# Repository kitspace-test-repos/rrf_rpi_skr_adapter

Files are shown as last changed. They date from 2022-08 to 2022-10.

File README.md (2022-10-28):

Raspberry Pi to SKR/SKR Pro Adapter for ReprapFirmware
======================================================

The adapter sold by TeamGloomy on Tindie for this purpose is sold out.  This
is my equivalent replacement.

Description
-----------

I'm looking at putting ReprapFirmware on my Hypercube 300.  The necessary
adapter to connect its Raspberry Pi Zero 2 W to its SKR Pro 1.2 is
out-of-stock on Tindie.  This is a smaller adapter that does the same thing,
only it plugs into the EXP2 header on the printer motherboard and a 6-wire
cable connects the other end to pins 19-24 on the Raspberry Pi GPIO header. 
(I already have a 4-wire UART connection between the two that also supplies
power; instead of putting in the full 40-pin GPIO header, it only has enough
pins populated for the connections I'm using.)

It was a quick layout to throw together in KiCad; I probably spent more time
playing around with panelization options than on the main layout.  :) I
should have 100 (20x5) bare boards arriving from JLCPCB, and the parts to go
on it are dirt-cheap…should be well under $5 from DigiKey, and probably
under $1 each in quantity from LCSC.

This project is also on
[printables.com](https://www.printables.com/model/262089-raspberry-pi-to-skrskr-pro-adapter-for-reprapfirmw).

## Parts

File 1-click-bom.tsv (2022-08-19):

References | Qty | Description | DigiKey_SKU | Inv_ID | LCSC_SKU | MPN | Manufacturer | Mouser_SKU | Notes | Package
J1 | 1 | Connector Header Through Hole, Right Angle 2x3 position 0.100" (2.54mm) | 2057-PH2RA-06-UA-ND | 60 | C706884 | PH2RA-06-UA | Adam Tech |  | LCSC SKU is substitute:: XKB X6521WR-2x03H-C30D60
J2 | 1 | 2x5 Position Header Connector 0.100" (2.54mm) Through Hole, Right Angle Gold | S9202-ND | 61 | C239356 | SFH11-PBPC-D05-RA-BK | Sullins Connector Solutions |  | LCSC SKU is substitute: CJT A2541HWR-2x5P
R1, R2, R3, R4, R5 | 5 | 100 Ω 0603 resistor | 311-100HRCT-ND | 49 | C105588 | RC0603FR-07100RL | Yageo | 603-RC0603FR-07100RL |  | 0603

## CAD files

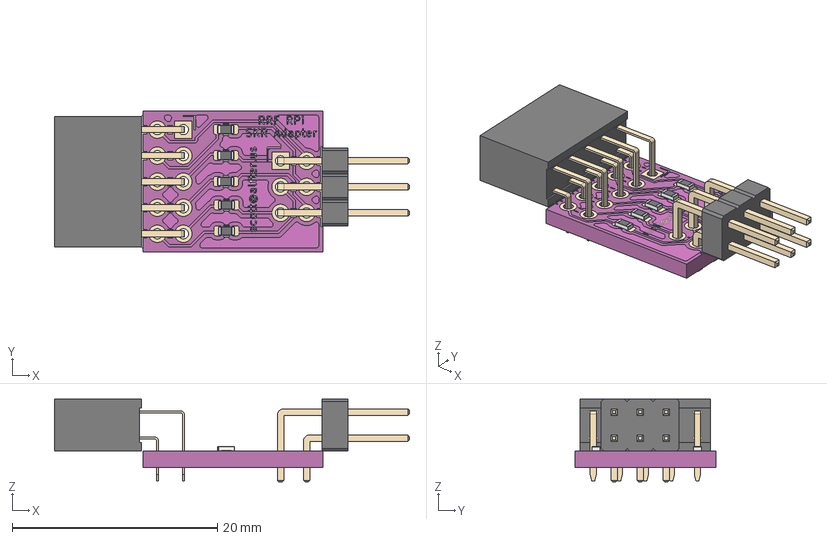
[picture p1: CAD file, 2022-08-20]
rrf_rpi_skr_adapter.step
34.6 x 13.7 x 8.08 mm
Pcb_c4a0
topPads_c4a0
topTracks_c4a0
topZones_c4a0
botPads_c4a0
botZones_c4a0
topSilks_d746
R5_R_0603_1608Metric_efb6d9ae4d17 x 5
J2_PinSocket_2x05_P254mm_Horizontal_7ad49dfecfbd
J1_PinHeader_2x03_P254mm_Horizontal_a65a8578a4f9

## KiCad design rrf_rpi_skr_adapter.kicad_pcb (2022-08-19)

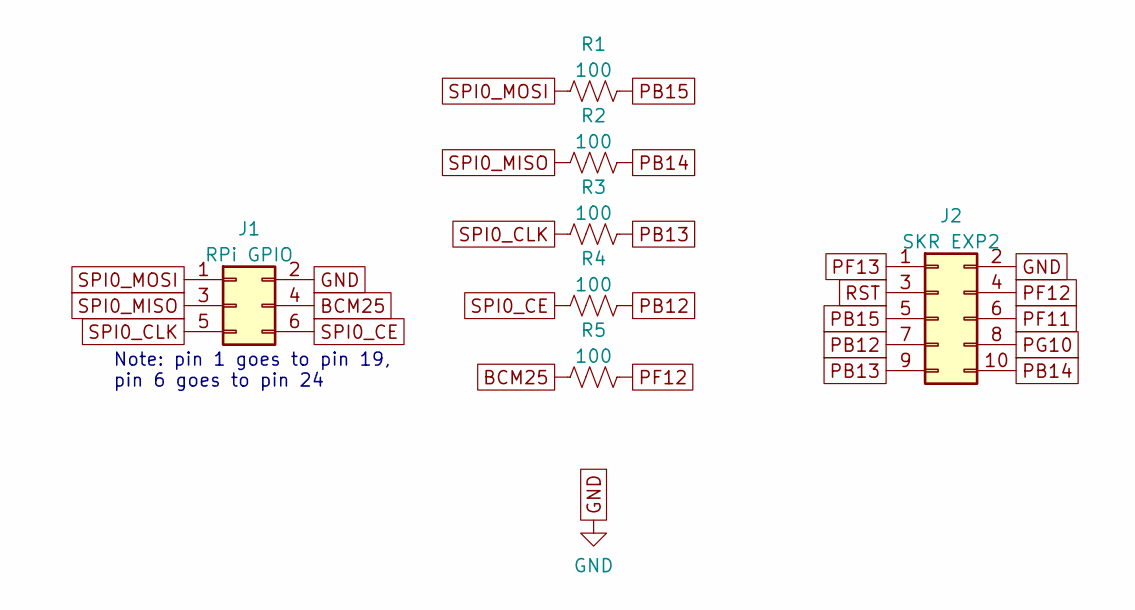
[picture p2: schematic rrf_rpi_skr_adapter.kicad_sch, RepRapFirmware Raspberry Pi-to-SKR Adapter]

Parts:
J1: RPi GPIO; PinHeader_2x03_P2.54mm_Horizontal; MPN PH2RA-06-UA; DigiKey_SKU 2057-PH2RA-06-UA-ND
J2: SKR EXP2; PinSocket_2x05_P2.54mm_Horizontal; MPN SFH11-PBPC-D05-RA-BK; DigiKey_SKU S9202-ND
R1, R2, R3, R4, R5: 100; R_0603_1608Metric; MPN RC0603FR-07100RL; DigiKey_SKU 311-100HRCT-ND

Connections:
BCM25: J1.4, R5.1
GND: J1.2, J2.2
PB12: J2.7, R4.2
PB13: J2.9, R3.2
PB14: J2.10, R2.2
PB15: J2.5, R1.2
PF11: J2.6
PF12: J2.4, R5.2
PF13: J2.1
PG10: J2.8
RST: J2.3
SPI0_CE: J1.6, R4.1
SPI0_CLK: J1.5, R3.1
SPI0_MISO: J1.3, R2.1
SPI0_MOSI: J1.1, R1.1

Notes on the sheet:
Note: pin 1 goes to pin 19, pin 6 goes to pin 24

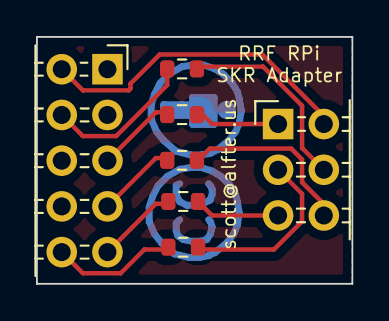
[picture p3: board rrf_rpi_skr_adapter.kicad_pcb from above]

Board: 2 copper layers, 17.5 x 13.7 mm, 7 parts (0 on the bottom side), 11 nets.

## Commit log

2022-08-20 add rendering
    [rrf_rpi_skr_adapter.step]
2022-12-01 separate panelized gerbers into their own directory for Kitspace
    [rrf_rpi_skr_adapter-panel-B_Cu.gbr, rrf_rpi_skr_adapter-panel-B_Mask.gbr, rrf_rpi_skr_adapter-panel-B_Silkscreen.gbr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]
